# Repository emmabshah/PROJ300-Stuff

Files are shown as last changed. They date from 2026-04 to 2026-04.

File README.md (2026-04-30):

This repository contains some of the main features of Freddy, specifically software-related aspects mentioned throughout the report. 

•	Custom Parrot Voice - contains Freddy's custom trained voice model

•	Final CAD STLs - contains all CAD STL files for Freddy

•	Freddy Main Code - contains the main Freddy script that runs on the Pi

•	General Proj Docs - contains past submitted Proj-related documents like Proposals, Powerpoints, etc

•	Loggeed Test Data - contains the logged data when testing Freddy

•	Porcupine - contains the custom 'Hey Freddy' wake-word model 

•	Servos - contains the servo calibration code

•	TextyMcSpeechy Linux Screenshots - contains all the Linux code used for TextyMcSpeechy to generate the voice

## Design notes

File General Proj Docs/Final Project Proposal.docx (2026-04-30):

Project Title: Wearable Robot Puppet with Eye-Blinking and Tracking using Computer Vision

Proposer: Self (in collaboration with an Arts University Plymouth Final Year Student)

Supervisor: Dena Bazazian

Objective:

- The main objective of this project is to design and develop an animatronic head for the Arts University students’ wearable puppet, inspired by a dragon-like creature.
- The ultimate goal is to bring their puppet to life through realistic moveable eyeballs and eyelids and a moveable beak which opens and closes using servos for actuation and computer vision for person-detection and tracking. The final design would be as one complete structure allowing ease for the student to place within their puppet.

Staged Deliverables (at least 4):

PASS (40%+):

To achieve a functioning physical prototype of the eyes, beak and eye covering and simulation of its expected movement. This includes:

- Fusion 360 CAD modelling and technical drawings of the eyes, beak, servo mounts, battery and microcontroller housings, and eye covering plate.
- Incorporating camera placement in the pupil/ above eye.
- Fusion 360 animating to simulate expected movement (blink, move eyeball, open and close beak).
- 3D-printing parts with iterative design documentation.
- Fitment check with artist’s puppet structure.

2:2 Mark (50%+)

To achieve mechanical actuation of motion. This includes:

- Calibrating servos.
- Servo mapping and forward kinematics.
- Programming servo movement to make:
  - Eyes blink (1DOF)
  - Eyeballs move (2DOF)
  - Beak open and close (1DOF)
- Controlling the movement on ESP32 microcontrollers and PWM drivers.
- Creating a standard looped movement sequence for the eyes and beak. This is intended to be used in more crowded environments.

2:1 Mark (60%+)

To achieve person-detection with the vision system. This includes:

- Operating the ESP32-CAM modules.
- Person-detection using computer vision.
- Testing across different lighting.
- Sending data to ESP32 board.

FIRST CLASS Mark (70%+)

To achieve full integration of both the mechanical and vision system. This includes:

- Mapping camera data to servo movements to allow eye tracking of people.
- Independent tracking for each eye (since they sit on opposite sides of the head).
- Additional enhancements such as synchronized sound with beak motion or refined eye movement mimicking the expression of the person being tracked.
- Professional finish and detailed documentation of design process and testing.
- Have the option of controlling the eyes via joystick.

Description:

This project aims to combine robotics, art, and performance by creating a wearable robotic puppet head that responds dynamically to people. The system will feature realistic eye blinking, motion tracking, and beak articulation, controlled through small servos and ESP32 microcontroller.

Initially, CAD software (Fusion 360) will be used to design the eye and beak mechanisms. After simulation and refinement, parts will be 3D printed with PLA and assembled with servo mounts and control boards using various nuts and bolts. These will also undergo further refinement after fit checks.

The eyeballs themselves will move in 2DOF (up and down and left and right) and the eye lids which open and close (1 DOF). These would be actuated using 4 9g micro servos per eye. Each eye will be able to move independently. Their movement would be controlled using the PCA9685 PWM driver and ESP32 board.

It is intended that eyeball module is separate from one another, meaning each eye will have a dedicated ESP32, ESP32CAM, PWM driver, 4 servos and its own battery supply. The battery will potentially be a 6V battery pack but depending on the amount of current taken by the servos through testing, other means such as a Lipo and buck converter can be used.

The beak will also be actuated using one servo to open and close it, but this will potentially need a heavier MG996R servo for actuation. If the lighter micro servo will suffice, then that will be used instead.

The ESP32-CAM modules will enable person detection. The camera will be placed in the eyeball pupil or above the eyeball. The ESP32-CAM will send data to the ESP32, which will then send the mappings to the PWM driver, allowing the puppet’s eyes to follow a person’s movement.

All code will be developed in Arduino IDE, and iterative testing will be conducted. The final system will be designed for easy integration into an artist’s wearable puppet, allowing them to animate their creature during live performance.

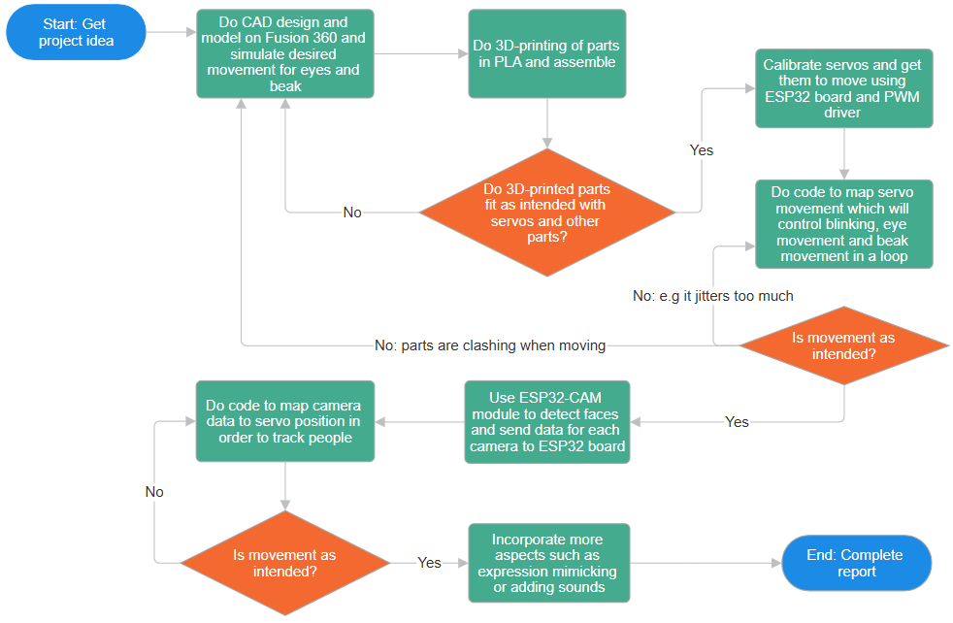
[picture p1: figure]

Figure 1: Flowchart Diagram of Project

Resources

- State assumptions about resources allocated to this project: Assume resources can be purchased within budget of £120.00
- Equipment: Power supply for testing, Laptop for CAD, 3D-printer for parts
- Locations: Lab
- Support & outside services: Lab techs
- Manufacturing: Not required

Schedule

- Deliverable 1 (Design and Simulation): By start of February (09/02/26)
- Deliverable 2 (Servo Actuation and Coding): By end of February (25/02/26)
- Progress Demonstration: February 26th, 2026
- Deliverable 3 (Vision System Integration): By middle of March (16/03/26)
- Deliverable 4 (Full Integration and Testing): By middle of April (13/04/26)

Related Documents

- Data Sheets:
1) 9G Micro Servos
- Web Pages: More to be included as research continues
1) Building a Robot that Sees (Through its Own Eyes): https://www.youtube.com/watch?v=IPBu5Q2aogE
2) Plymouth Owl: https://www.plymouth.ac.uk/research/robotics-neural-systems/plymouth-owl

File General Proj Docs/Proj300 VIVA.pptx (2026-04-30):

## PROJ300 VIVA

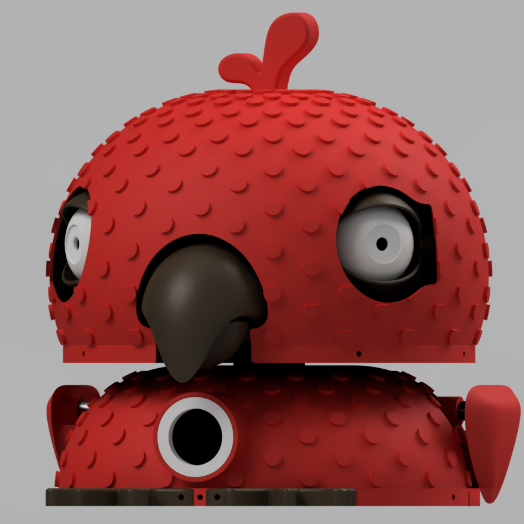
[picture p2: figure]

Interactive Parrot Robot with Face Tracking, Emotion Recognition and Voice Repetition
By Emma Shah

## Project Aim

Freddy was also designed to operate locally on the Raspberry Pi rather than relying on cloud services. This supported privacy, accessibility, and independence from internet connection.

- To create a characteristic animatronic robot that could:
- track a person’s face
- react to facial expressions
- listen for “Hey Freddy”
- repeat speech in a custom parrot voice
- move eyes, eyelids, wings, neck, beak, and LEDs

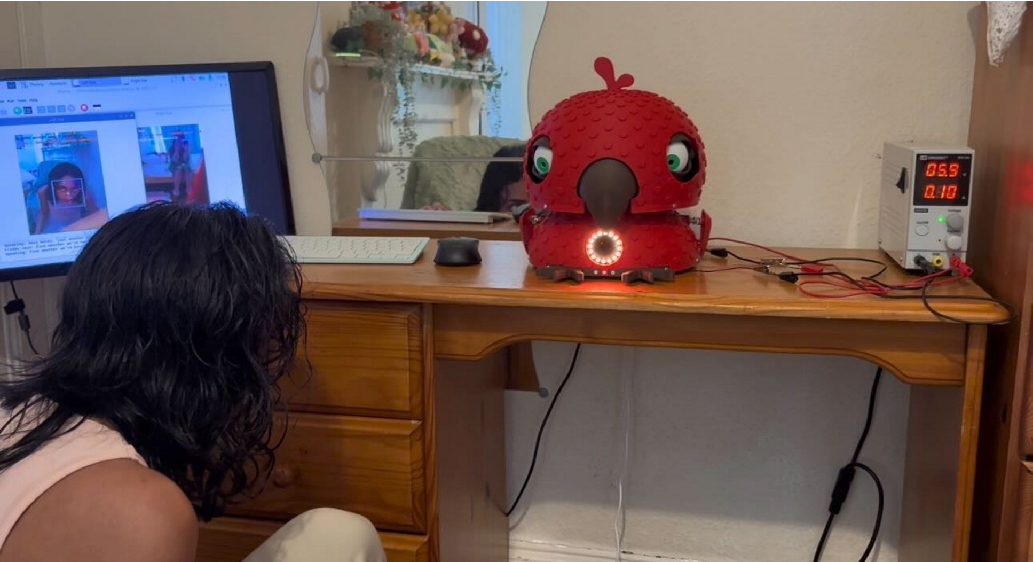
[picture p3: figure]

## Original vs Final Deliverables

Proposal stage | Original target | Final outcome
Pass | Physical prototype of eyes, beak, covering, CAD simulation, 3D prints, fitment checks | Achieved and expanded into a full animatronic parrot body with eyes, eyelids, beak, wings, neck, covering, fitment checks, CAD simulations, and final assembly
2:2 | Servo calibration and programmed motion for blinking, eyeball movement, and beak actuation | Achieved, with additional servo-driven wings, neck movement, beak animation, eyelids, and emotion-based motion behaviours
2:1 | Person detection using ESP32-CAM modules and testing in different lighting | Achieved using Raspberry Pi 5 and dual Pi cameras instead of ESP32-CAMs, with MediaPipe face detection and testing under different lighting/movement conditions
First | Camera data mapped to servo movement for independent eye tracking, plus enhancements such as sound/beak synchronisation and expressive behaviour | Achieved and expanded: face tracking controlled eyes and neck, while additional systems included emotion recognition, wake-word detection, speech transcription, custom Piper voice, beak animation, LEDs, and parrot mode

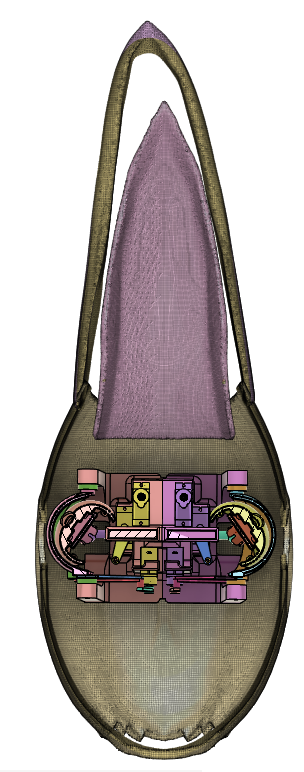
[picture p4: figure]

## System Overview

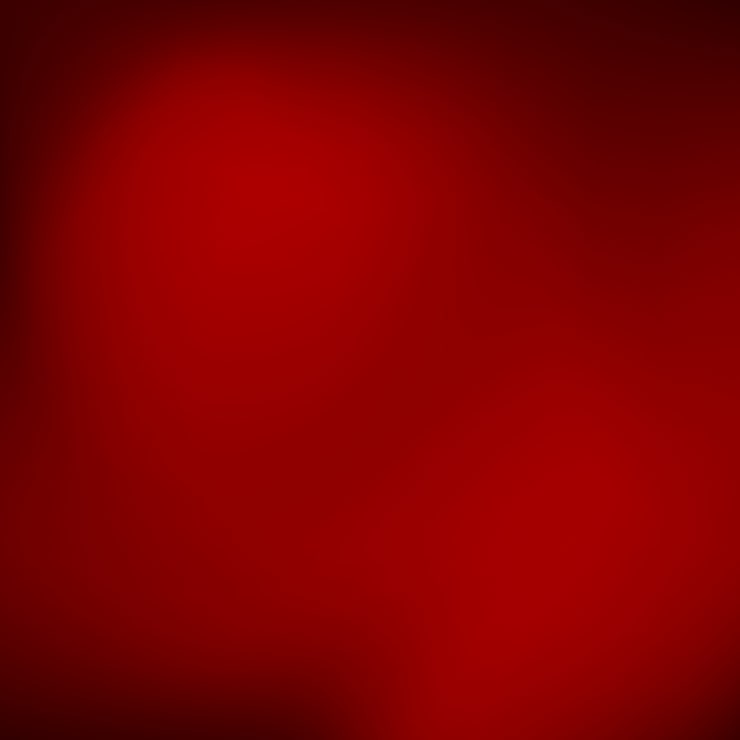
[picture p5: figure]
Red backdrop background Images - Free Download on Freepik
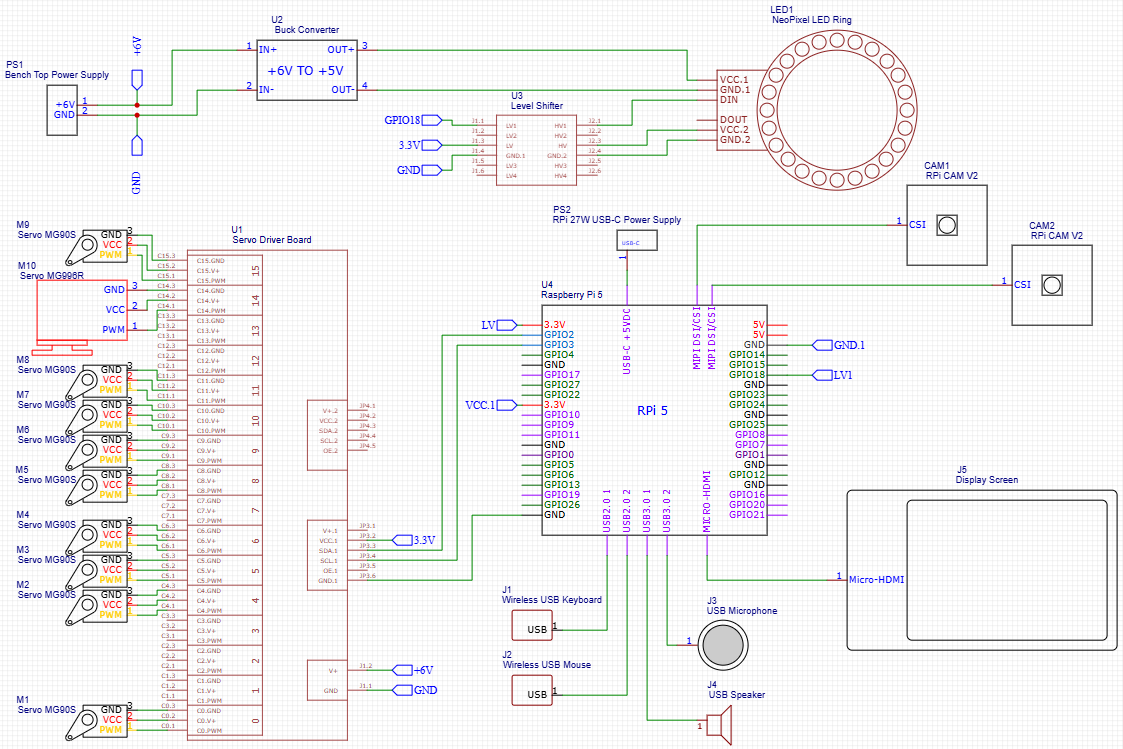
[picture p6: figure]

Freddy was built around a Raspberry Pi 5, which coordinated the vision, audio, and motion subsystems. Key components included:
- Two Raspberry Pi Camera Module 2 for face tracking
- A PCA9685 driver board for servo control
- Servos for the eyes, eyelids, beak, wings, and neck
- A NeoPixel LED ring for emotion feedback
- A microphone for wake-word detection and speech input
- A speaker for audio output
- Power regulation components including a buck converter
- Bi-directional logic level shifter to convert Pi 3.3V data output to 5V

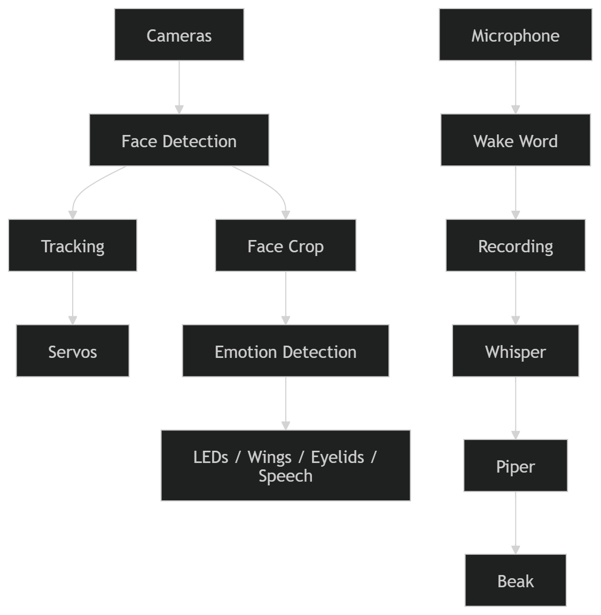
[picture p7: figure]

## Mechanical Design

Freddy was design in Fusion 360 and 3D-print in PLA. Most parts were 3D printed and designed from scratch.
The design involved:

- MG90S servo-driven eyes, eyelids, beak and wings
- MG996R servo-driven neck
- Mounts for the Pi, PCA9685, Speaker, Buck Convertor, Microphone
The design was the longest process as it involved lots of iteration through physical fitment tests.

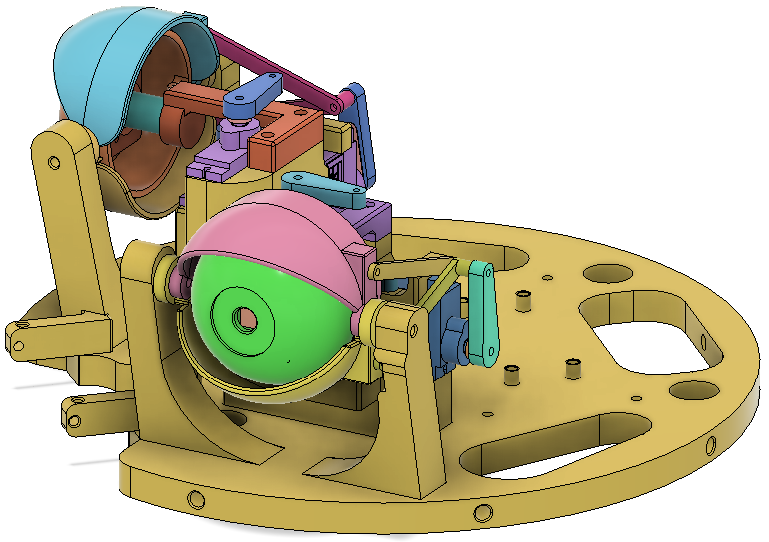
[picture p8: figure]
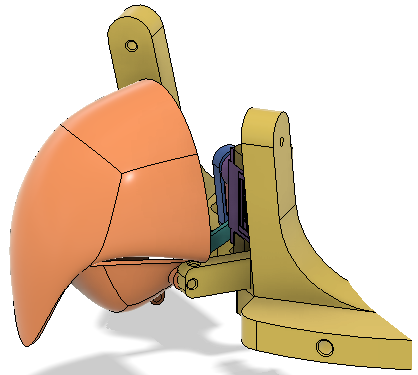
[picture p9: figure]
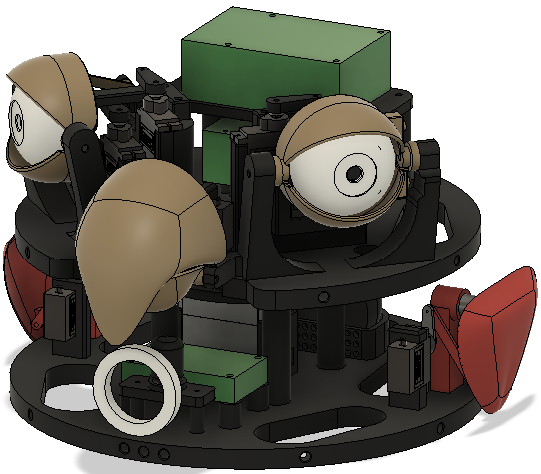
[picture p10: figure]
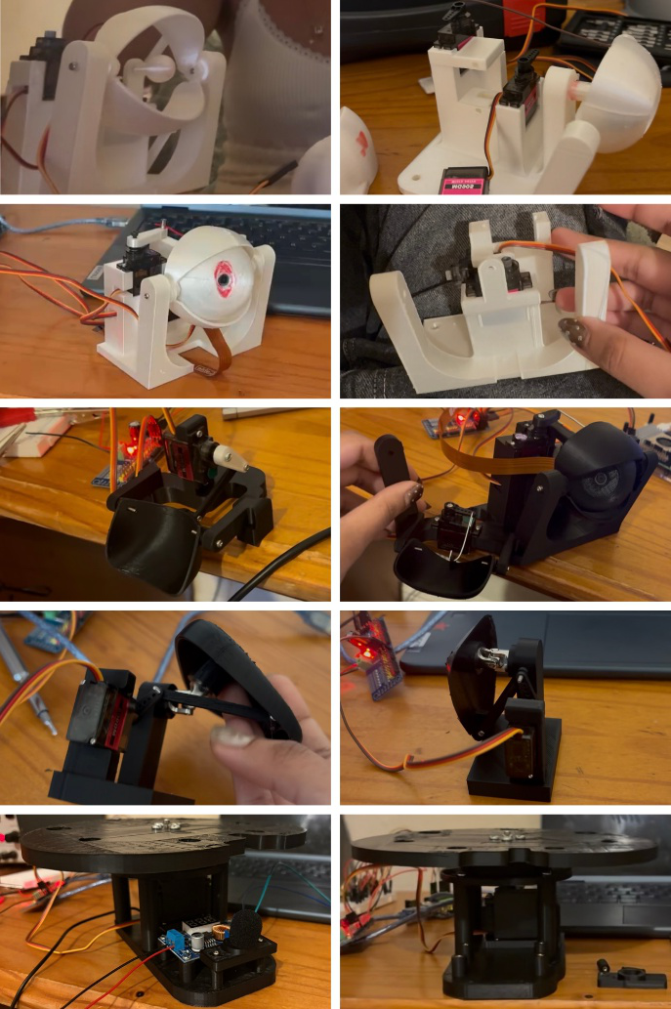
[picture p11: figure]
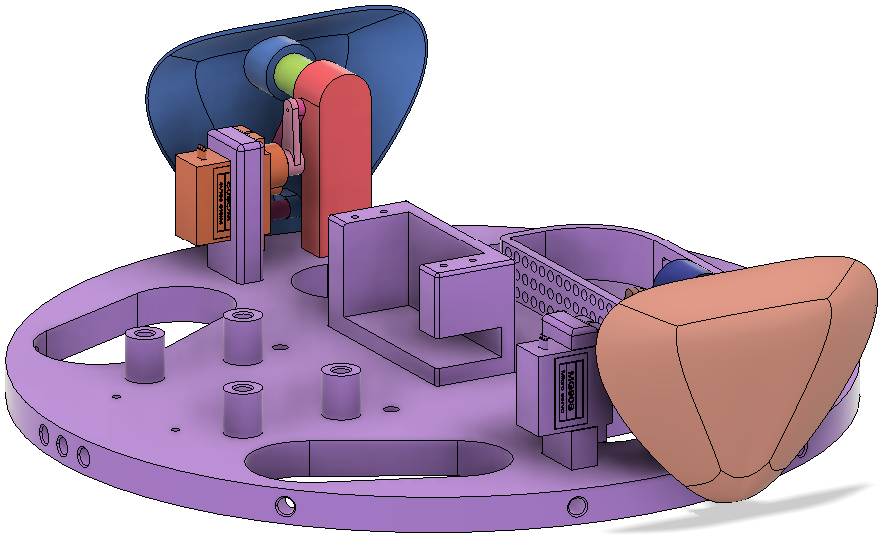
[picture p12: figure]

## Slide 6

Servo Calibration

Since servos do not know their true position, they had to be calibrated using a protractor to determine 0-180° motion.
Pulse Width Modulation (PWM) tick limits for each mechanism had to be found experimentally. An Arduino UNO, PCA9685 and potentiometers were used to do this, and final calibrated values were transferred into Python on the Pi.

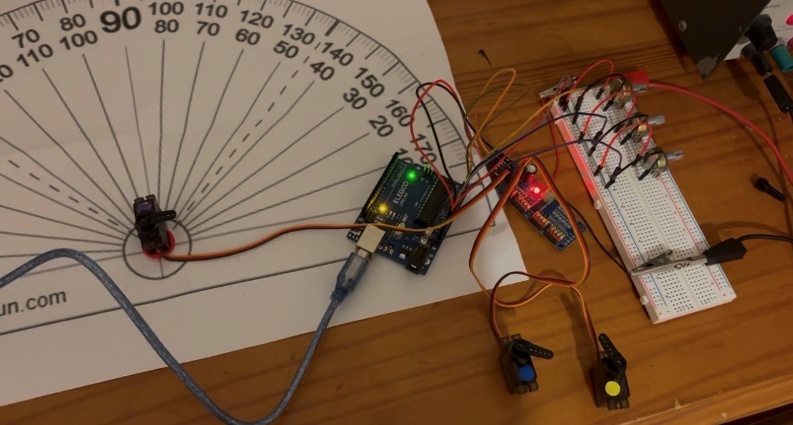
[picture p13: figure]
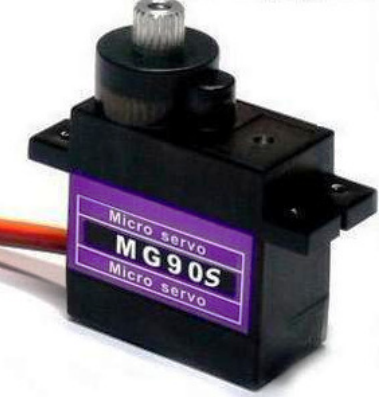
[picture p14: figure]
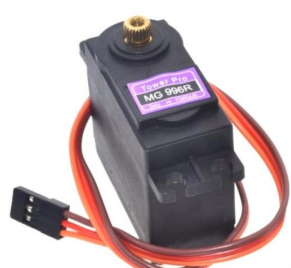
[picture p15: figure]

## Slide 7

Face Tracking

Freddy uses the cameras mounted as pupils in its eyeballs to track. It incorporates active target selection, proportional-style tracking, deadzones to reduce jitter and scanning when no face is detected.
For face detection, MediaPipe, an open-source framework from Google, was used. When a face was detected in the camera frame, the code compared that position to the centre of the frame and then moved the eyes and neck to reduce the error between the two.

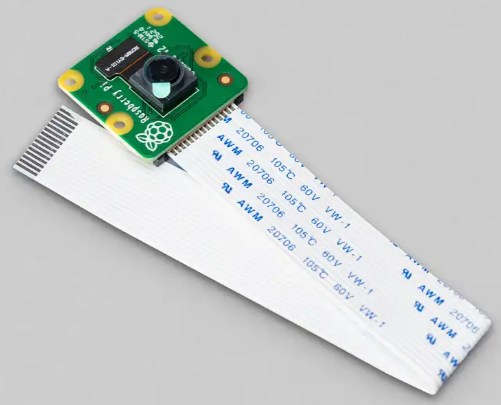
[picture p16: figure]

Testing:
With the confidence threshold = 0.5,
The tracking solution performed well with a normalised tracking error of 0.287 maximum and only 4 instances in which the face was not detected.

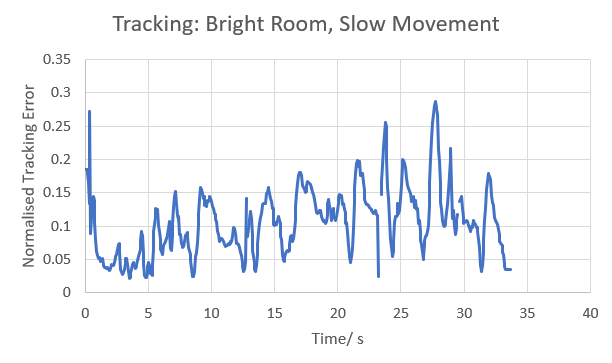
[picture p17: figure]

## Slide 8

Emotion Recognition

Freddy uses another open-source framework for emotion recognition: HSEmotion, specifically the model, enet_b0_8_best_afew. He can detect 7 out of the 8 emotions: happy, sad, angry, disgust, fear, surprise, neutral.

timestamp | raw_prediction | stable_emotion
1777036530 | disgust | neutral
1777036531 | disgust | neutral
1777036532 | disgust | disgust
1777036533 | disgust | disgust
1777036534 | disgust | disgust
1777036535 | disgust | disgust
1777036536 | disgust | disgust
1777036537 | disgust | disgust
1777036538 | disgust | disgust
1777036539 | disgust | disgust
1777036540 | disgust | disgust
1777036541 | disgust | disgust
1777036542 | disgust | disgust
1777036543 | disgust | disgust
1777036544 | disgust | disgust
1777036545 | disgust | disgust
1777036546 | angry | disgust
1777036547 | disgust | disgust
1777036548 | disgust | disgust
1777036549 | disgust | disgust

Essentially, a cropped face is passed to the model, raw predictions could flicker but with a confidence threshold, majority voting, and stability timer, behaviour was smoother.
Testing:
For an example of the stability working, this was a snippet of test data when detecting ‘disgust’.

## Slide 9

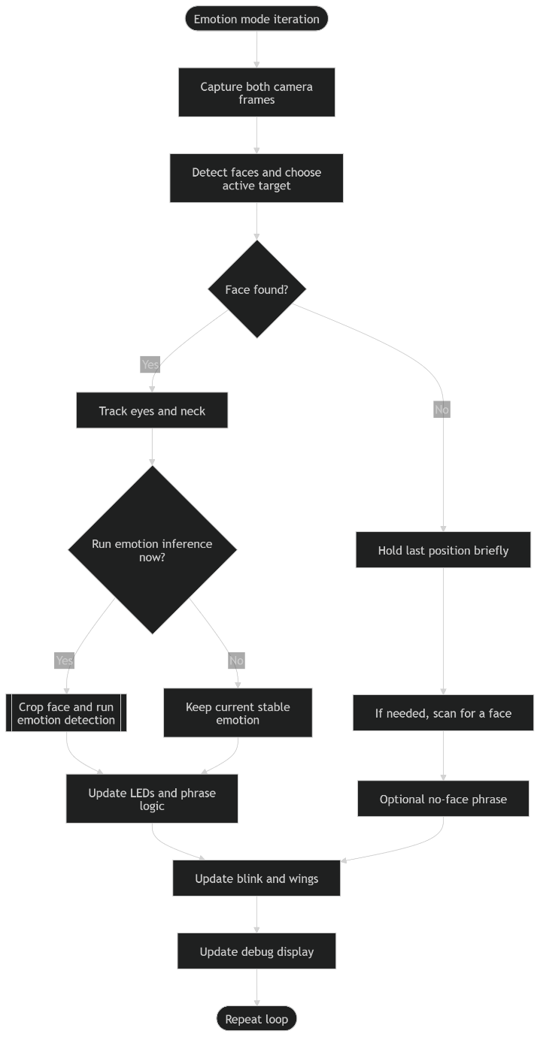
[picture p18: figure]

Modes

Freddy has two distinct modes of interaction:
1. Robot/ Emotion Mode: Freddy tracks the user’s face, recognises their emotion then responds with eyelid and wing movement, speech, and LED ring colour changes.
2. Parrot Mode: Freddy listens for the wake-word, “Hey Freddy”, transcribes spoken input with Whsiper STT, translates it into English, and repeats it aloud with Piper TTS.
Testing:
A big challenge with Freddy being local and offline, meant that latency was a potential issue. After testing, the Base Whisper Model was found to perform best in terms of balancing accuracy and latency, performing at 73% English transcription accuracy and approximately 4s transcription time.
Translation was still quite inaccurate though with a 30% accuracy.

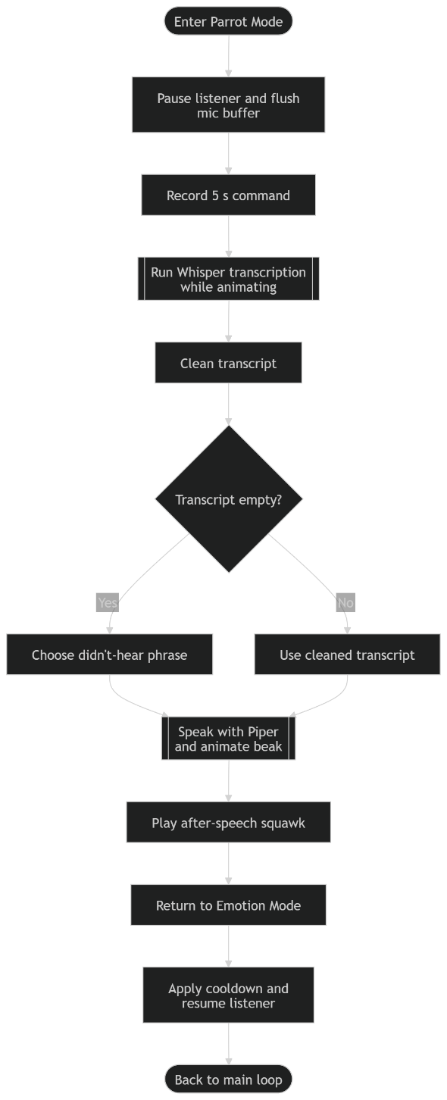
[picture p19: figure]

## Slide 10

Custom Voice

- ElevenLabs used was to establish desired voice style
- Chatterbox TTS was used to generated 1500 training clips from a metadata.csv file using the selected voice
- Training clips were manually checked
- An open-source framework, TextyMcSpeechy, was used to train the custom Piper voice for 5 hours
- Final voice model ran locally and offline

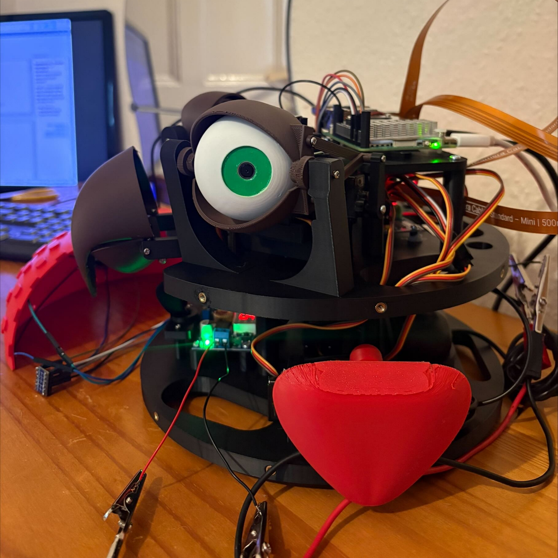
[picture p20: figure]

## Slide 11

Wake-word Detection

A framework called by Picovoice called Porcupine was used to generate the custom wake-word model, ‘Hey Freddy’.
Testing:
A sensitivity of 0.8 worked well for detection but false positives still existed with a 30% false positive detection rate.

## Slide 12

Why these models?

Component | Chosen option | Why
Face detection | MediaPipe | lightweight, real-time, gives bounding boxes
Emotion | HSEmotion | pre-trained, easier than training from scratch
STT | Whisper Base | best accuracy/ latency compromise
TTS | Piper | lightweight, local/ offline TTS
Wake word | Porcupine | more reliable than openWakeWord which was previously used

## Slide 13

Challenges

- Integrating many threaded subsystems: race conditions
- Servo calibration: tedious
- Cable routing issue: restricting neck motion
- Custom voice training: time-consuming
- Debugging hardware/ software together: figuring out whether servo jitter was code-related or a mechanical issue
- False wake-word triggers
- Latency and poor translation

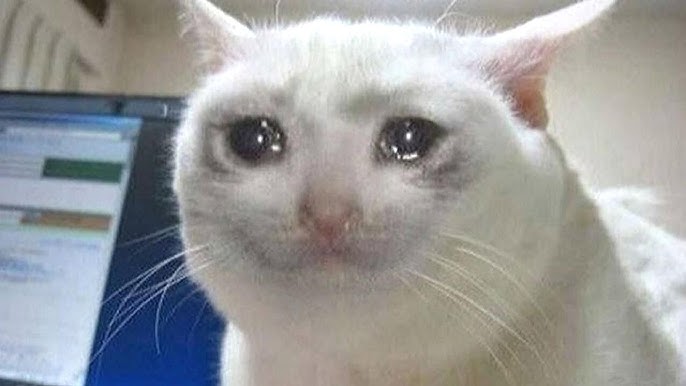
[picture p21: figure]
Sad Cats - Cute & Funny Cat Videos Compilation

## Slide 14

What I Learned

- New aspects about Fusion 360 CAD: forms, motion studies, tolerances, drawings
- How to use a 3D-printer: fitment check
- How to use a Raspberry Pi for a robotics project
- Linux, virtual environments, terminal commands, and dependency installation
- Experience in integrating pre-trained ML models
- Improved confidence in handling unfamiliar technical problems

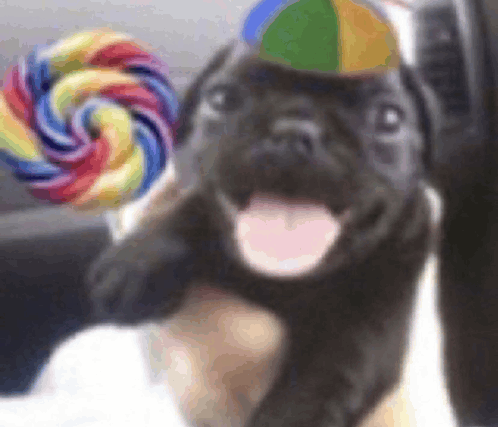
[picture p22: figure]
Happy Dog With A Lollipop Meme - Happy dog with a lollipop - Discover & Share GIFs

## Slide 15

Future Improvements

- Get a better microphone
- AI accelerator HAT for faster offline models
- Modular code structure rather than one giant script
- Raspberry Pi-based servo calibration script
- Better neck cable routing
- Physical start/ stop button
- Belly LCD display for transcription/ status
- Voice activity detection instead of fixed 5s recording
- Possible local LLM for replies instead of pre-determined phrases

## Demo

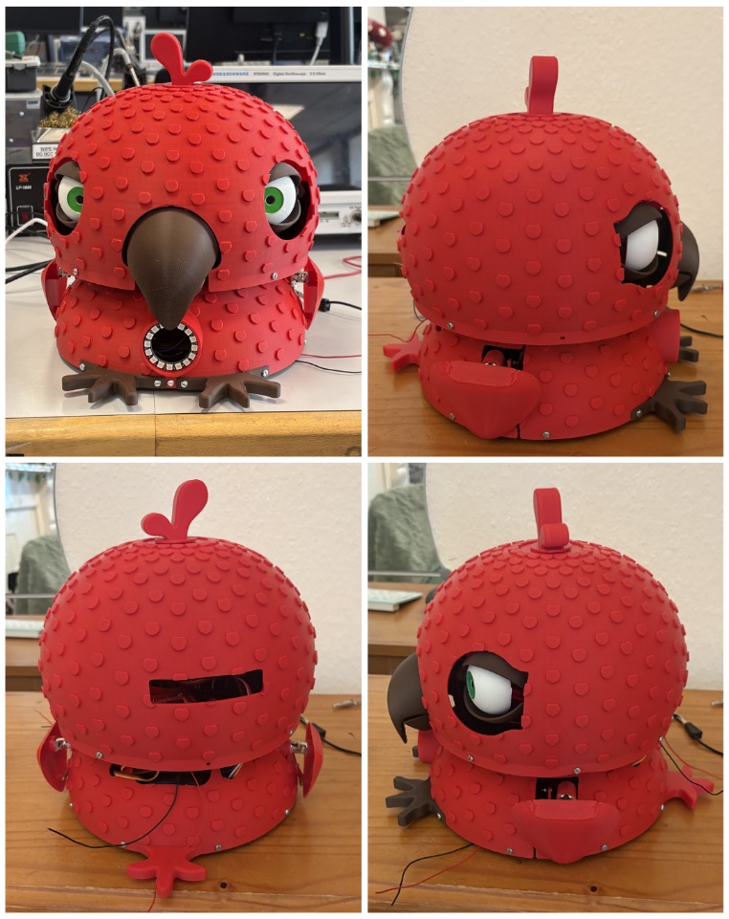
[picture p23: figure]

## Feedback

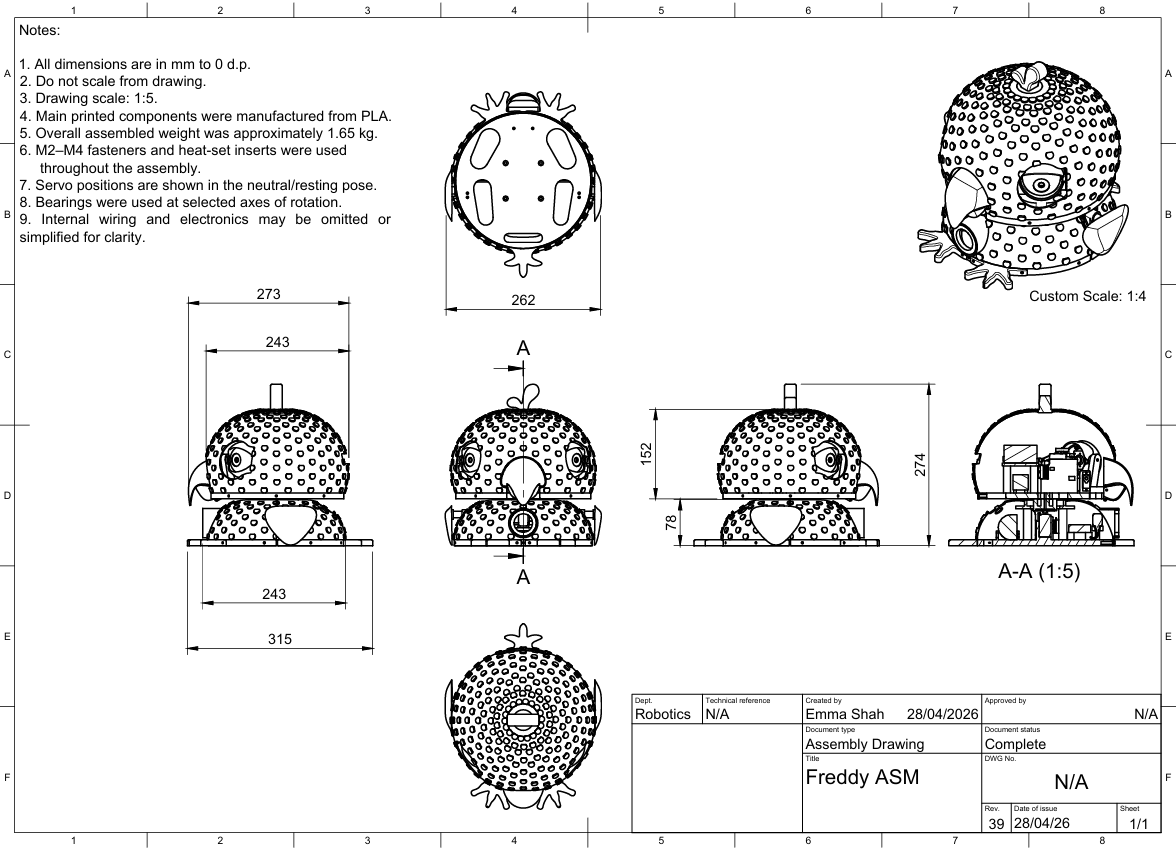
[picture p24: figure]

If you have any questions, please do let me know!

## THANK YOU

Emma Shah

1,600+ Smiley Face Thumbs Up Stock Photos, Pictures & Royalty-Free Images - iStock | Smiley face icon

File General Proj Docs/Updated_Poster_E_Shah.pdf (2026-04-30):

# IInntteerraaccttiivveePPaarrrroottRRoobboott

wwiitthhFFaacceeTTrraacckkiinngg,,EEmmoottiioonnRReeccooggnniittiioonnaannddVVooiicceeRReeppeettiittiioonn

# “Hey Freddy”

# “Hey Freddy”

Emma Shah
emmabshah@gmail.com

BEng (Hons) Robotics, University of Plymouth Dena Bazazian (Supervisor) www.linkedin.com/in/emmabshah

### Overview

Freddy is an interactive parrot-inspired animatronic robot that runs locally and offline on a Raspberry Pi 5. Designed in Fusion 360, built using 3D-printed parts, and actuated with MG90S and MG996R servos, Freddy aims to provide engaging entertainment and educational interaction without relying on cloud services.

### Overview

Freddy is an interactive parrot-inspired animatronic robot that runs locally and offline on a Raspberry Pi 5. Designed in Fusion 360, built using 3D-printed parts, and actuated with MG90S and MG996R servos, Freddy aims to provide engaging entertainment and educational interaction without relying on cloud services.

### Technical Features

Freddy was coded in Python, using open-source libraries such as MediaPipe for face detection, HSEmotion for emotion recognition, and Whisper for speech-to-text transcription. It also uses a custom Piper voice for text-tospeech, trained on ElevenLabs-generated audio. Additionally, the wake-word model was generated using Porcupine.

### Technical Features

Freddy was coded in Python, using open-source libraries such as MediaPipe for face detection, HSEmotion for emotion recognition, and Whisper for speech-to-text transcription. It also uses a custom Piper voice for text-tospeech, trained on ElevenLabs-generated audio. Additionally, the wake-word model was generated using Porcupine.

### How to Interact with Freddy

### 1. Robot Mode (Default): Freddy tracks the user’s face using two

Raspberry Pi Camera Module 2 cameras mounted in its eyes and recognises seven emotions. It then responds with eyelid and wing movement, speech, and LED ring colour changes.

### 2. Parrot Mode: Freddy listens for a wake word, transcribes spoken

input, translates it into English, and repeats it aloud. Simply say “Hey Freddy” to activate Parrot Mode.

### How to Interact with Freddy

### 1. Robot Mode (Default): Freddy tracks the user’s face using two

Raspberry Pi Camera Module 2 cameras mounted in its eyes and recognises seven emotions. It then responds with eyelid and wing movement, speech, and LED ring colour changes.

### 2. Parrot Mode: Freddy listens for a wake word, transcribes spoken

input, translates it into English, and repeats it aloud. Simply say “Hey Freddy” to activate Parrot Mode.

Buck Converter, Level Shifter, MG90S and PCA9685 Images from Amazon.com Raspberry Pi 5 and Raspberry Pi Camera Module 2 Images from ThePiHut.com

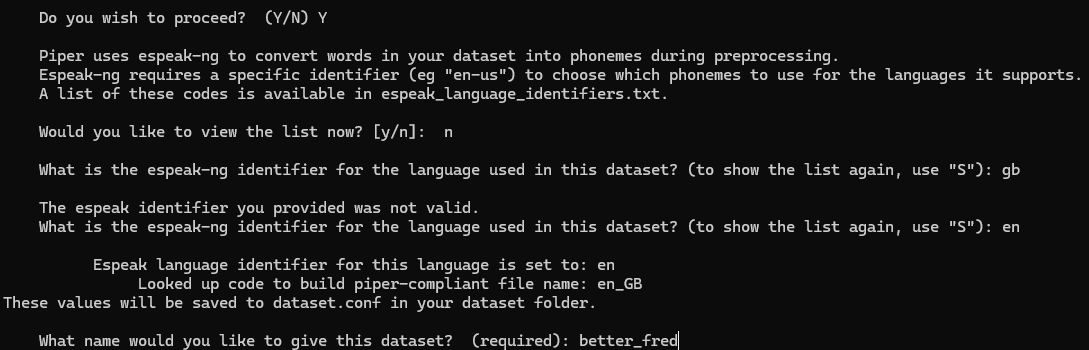
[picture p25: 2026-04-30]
TextyMcSpeechy Linux Screenshots/Screenshot21.png

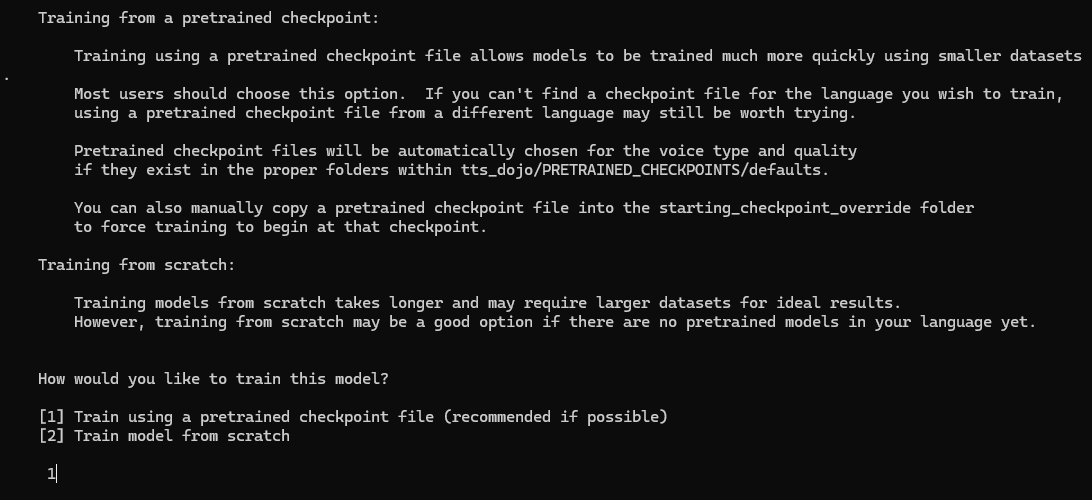
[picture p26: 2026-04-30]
TextyMcSpeechy Linux Screenshots/Screenshot30.png

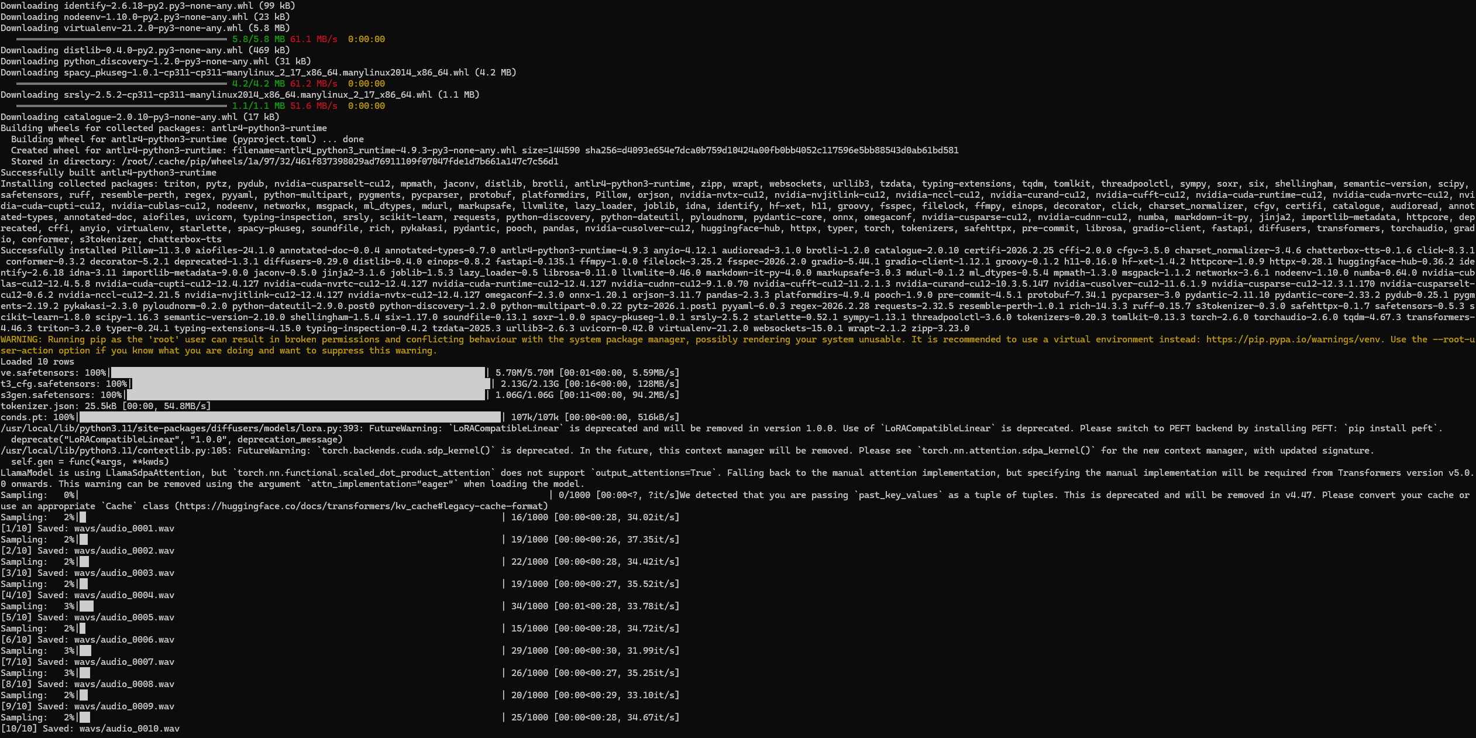
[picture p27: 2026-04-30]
TextyMcSpeechy Linux Screenshots/Screenshot5.png

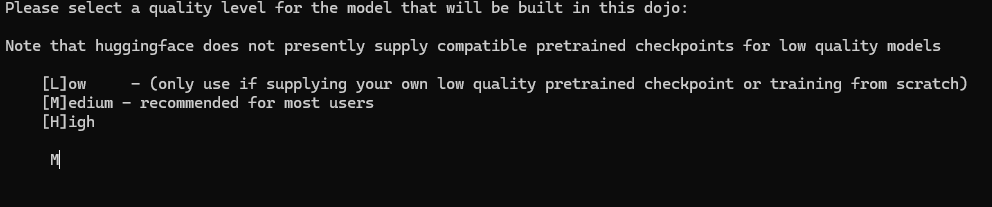
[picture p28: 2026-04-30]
TextyMcSpeechy Linux Screenshots/Screenshot29.png

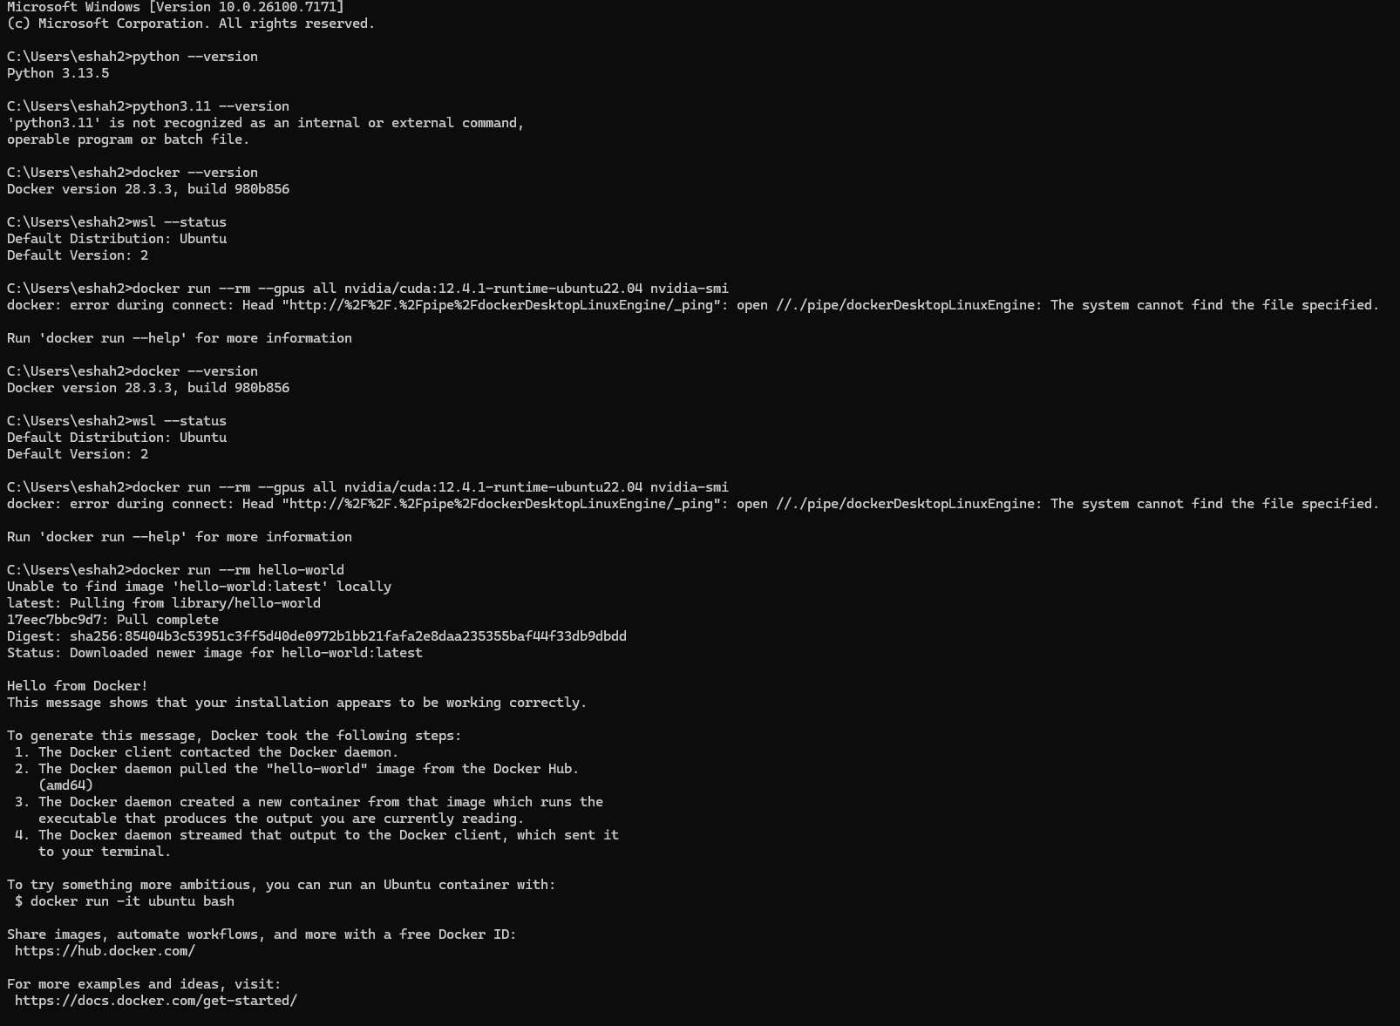
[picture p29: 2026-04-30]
TextyMcSpeechy Linux Screenshots/Screenshot1.png

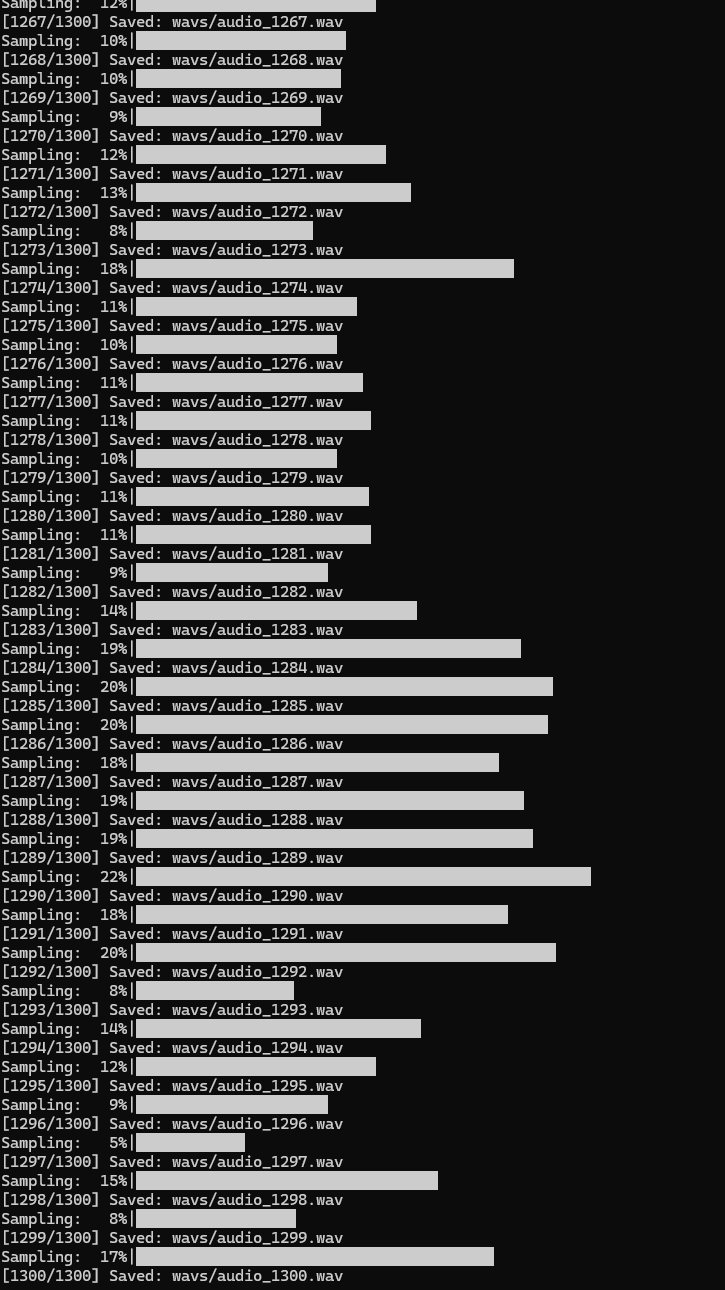
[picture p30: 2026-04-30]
TextyMcSpeechy Linux Screenshots/Screenshot6.png

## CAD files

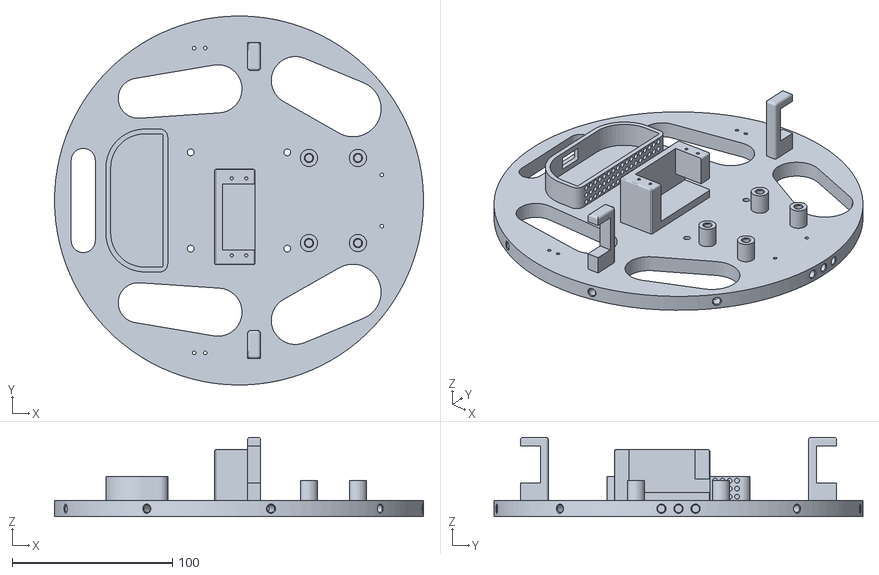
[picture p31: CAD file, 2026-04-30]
Final CAD STLs/Black or whatever colour/Body base.stl
230.0 x 230.0 x 49.5

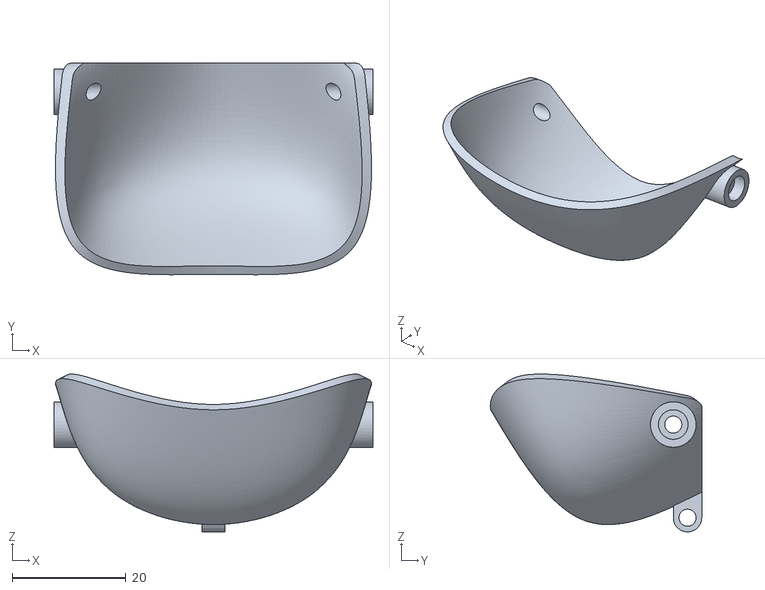
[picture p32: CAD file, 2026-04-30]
Final CAD STLs/Brown/Bottom beak.stl
56.0 x 37.1 x 27.7

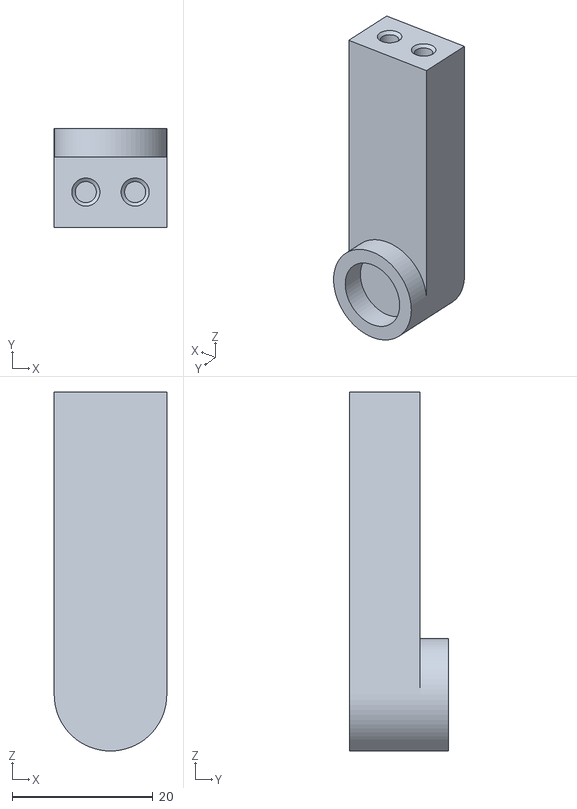
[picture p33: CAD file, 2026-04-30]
Final CAD STLs/Red/Wing joint holder (x2).stl
16.0 x 14.0 x 51.0

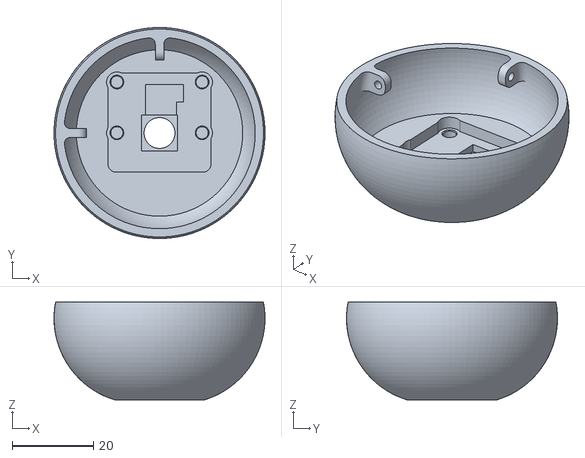
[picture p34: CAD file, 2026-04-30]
Final CAD STLs/White/Right eyeball.stl
52.0 x 52.0 x 24.1

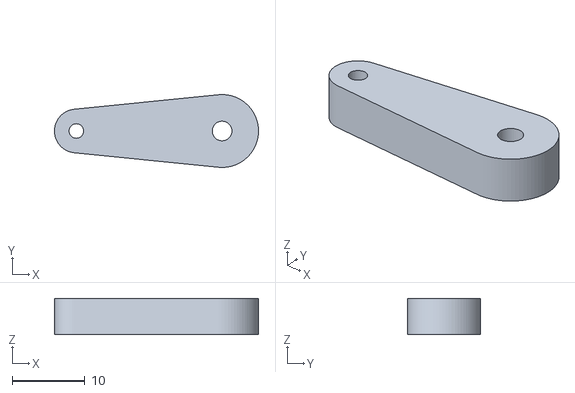
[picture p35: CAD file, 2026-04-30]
Final CAD STLs/Black or whatever colour/Servo horn extender short (x4).stl
28.0 x 10.00 x 5.00

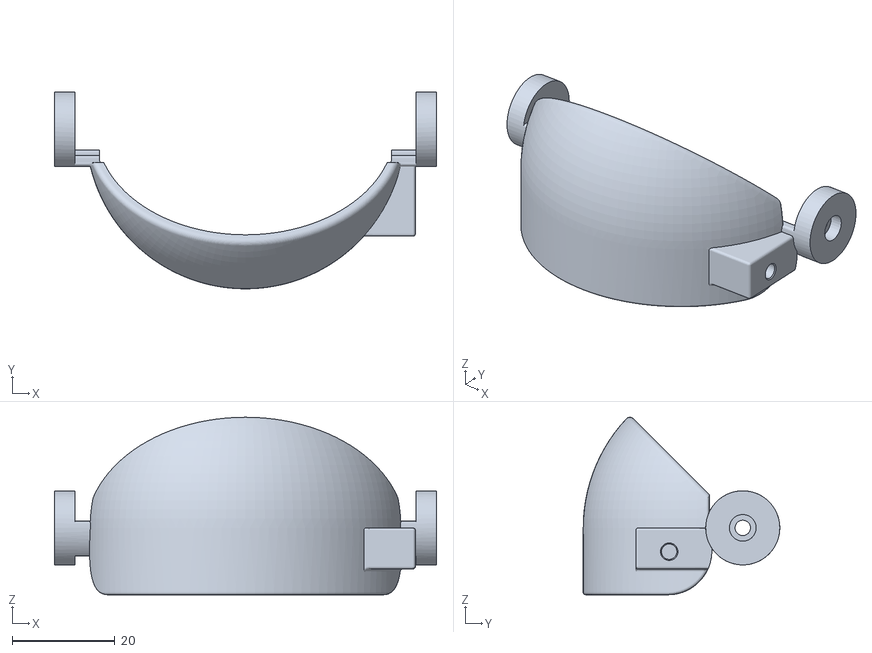
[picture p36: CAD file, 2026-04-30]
Final CAD STLs/Brown/Left lower eyelid.stl
74.2 x 38.2 x 34.5

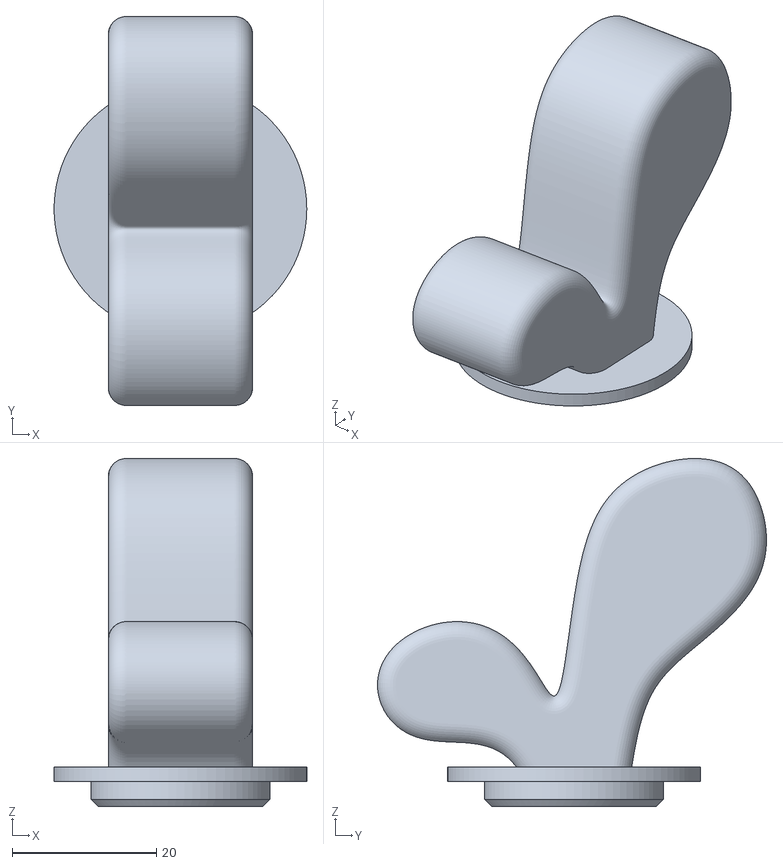
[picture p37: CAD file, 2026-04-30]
Final CAD STLs/Red/Top head feather.stl
35.0 x 53.9 x 48.2

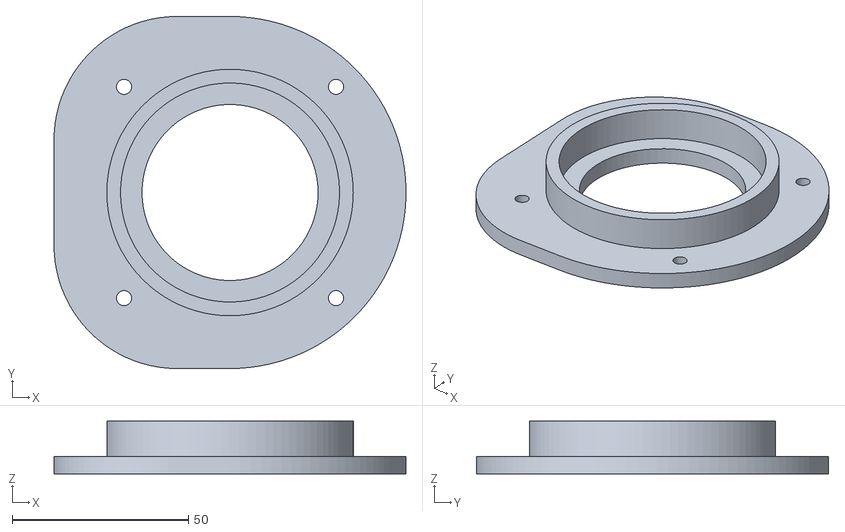
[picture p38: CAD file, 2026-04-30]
Final CAD STLs/Black or whatever colour/Neck bearing holder.stl
100.0 x 100.0 x 15.0

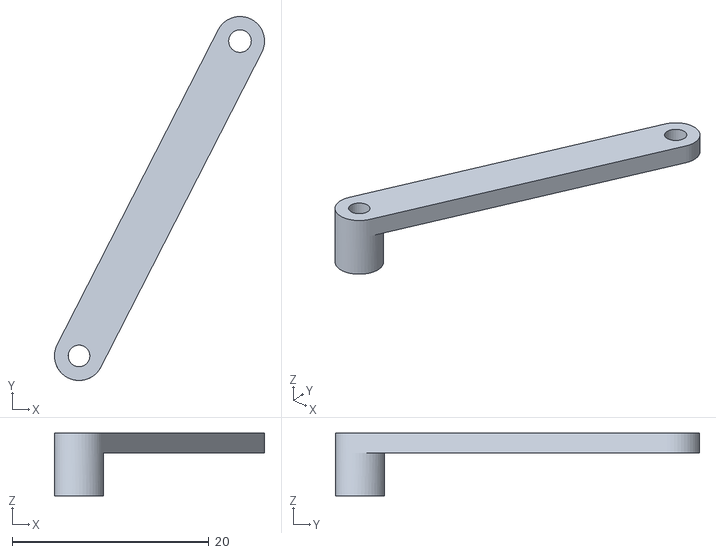
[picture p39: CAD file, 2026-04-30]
Final CAD STLs/Brown/Bottom beak link.stl
21.3 x 37.0 x 6.39

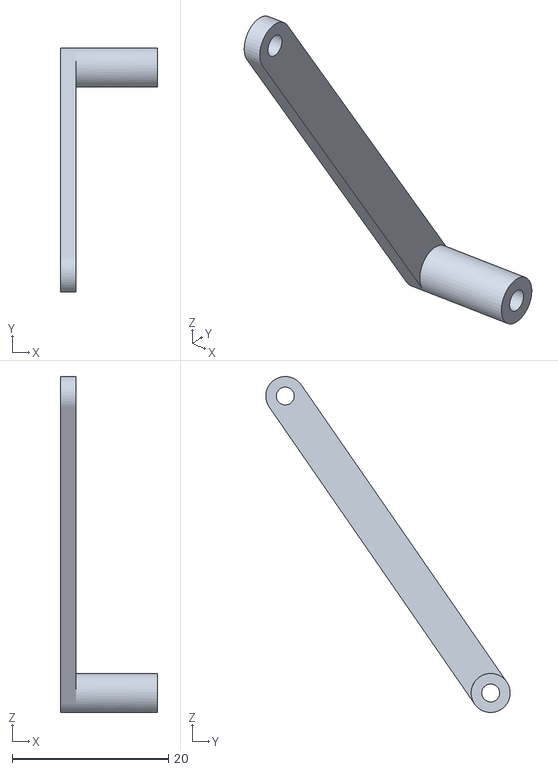
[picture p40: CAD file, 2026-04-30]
Final CAD STLs/Red/Wing link (x2).stl
12.5 x 31.3 x 43.0

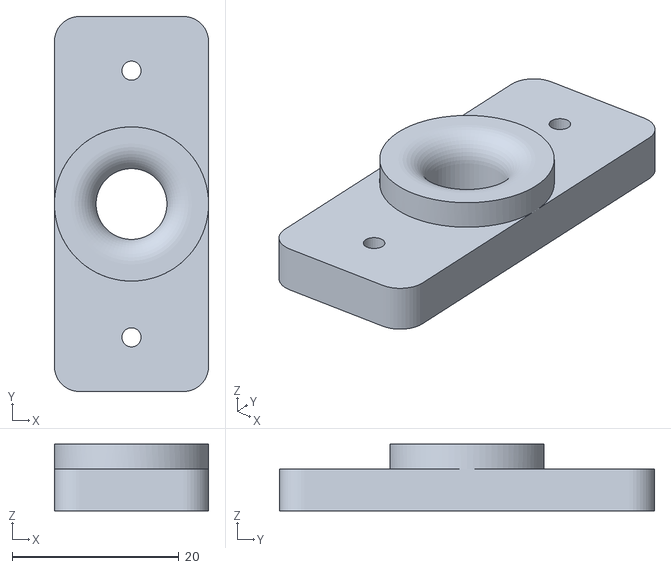
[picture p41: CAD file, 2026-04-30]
Final CAD STLs/Black or whatever colour/Mic holder.stl
18.5 x 45.0 x 8.00

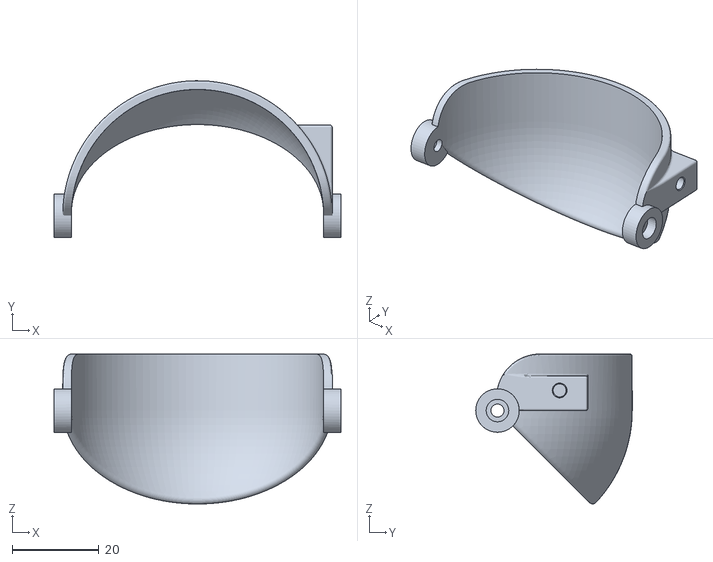
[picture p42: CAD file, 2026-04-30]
Final CAD STLs/Brown/Right upper eyelid.stl
66.0 x 36.0 x 34.5

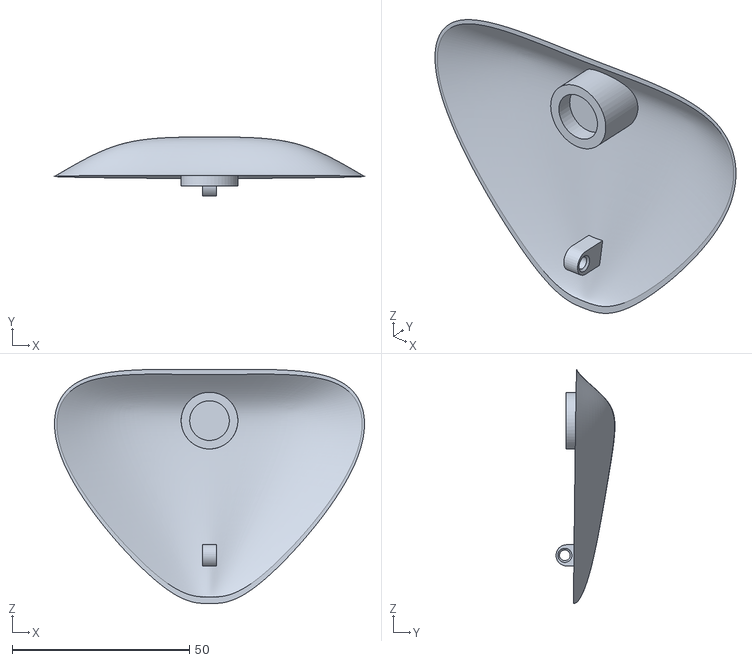
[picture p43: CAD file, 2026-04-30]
Final CAD STLs/Red/Left wing.stl
87.5 x 16.6 x 66.1

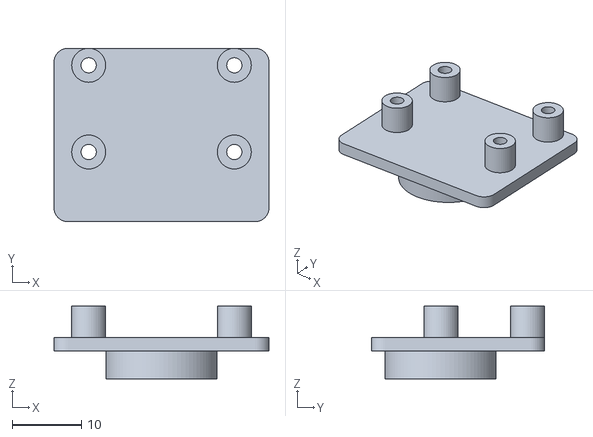
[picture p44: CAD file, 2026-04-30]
Final CAD STLs/Black or whatever colour/Eye joint holder (x2).stl
31.0 x 25.0 x 10.5

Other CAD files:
Final CAD STLs/White/Left eyeball updated.stl
Final CAD STLs/Brown/Right foot updated.stl
Final CAD STLs/Red/Right wing.stl
Final CAD STLs/Black or whatever colour/Servo horn extender middle (x2).stl
Final CAD STLs/Black or whatever colour/Body cylinder (4x).stl
Final CAD STLs/Black or whatever colour/Head cylinder (4x).stl
Final CAD STLs/Black or whatever colour/Head plate.stl
Final CAD STLs/Black or whatever colour/Left joint holder.stl
Final CAD STLs/Black or whatever colour/Mic cylinder (x2).stl
Final CAD STLs/Black or whatever colour/Neck cylinder update V2.stl
Final CAD STLs/Black or whatever colour/Neck cylinder.stl
Final CAD STLs/Black or whatever colour/Pi plate.stl
Final CAD STLs/Black or whatever colour/Right joint holder.stl
Final CAD STLs/Brown/Bottom eye link (x2).stl
Final CAD STLs/Brown/Left foot updated.stl
Final CAD STLs/Brown/Left upper eyelid.stl
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

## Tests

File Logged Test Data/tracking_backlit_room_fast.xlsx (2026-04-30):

timestamp | elapsed_s | condition | active_cam | has_face | face_x | face_y | centre_x | centre_y | error_x | error_y | error_dist | norm_error_dist | frame_w | frame_h | l_pan_norm | r_pan_norm | tilt_norm | neck_ticks
1777032181 | 0.001 | backlit_room_fast | L | TRUE | 124 | 200 | 240 | 320 | -116 | -120 | 166.9 | 0.2086 | 480 | 640 | 0.058 | 0 | -0.045 | 230 | MAX | 0.2086
1777032181 | 0.148 | backlit_room_fast | L | TRUE | 126 | 198 | 240 | 320 | -114 | -122 | 167 | 0.2087 | 480 | 640 | 0.115 | 0 | -0.0907 | 230
1777032181 | 0.19 | backlit_room_fast | L | TRUE | 126 | 195 | 240 | 320 | -114 | -125 | 169.2 | 0.2115 | 480 | 640 | 0.172 | 0 | -0.1376 | 230
1777032181 | 0.226 | backlit_room_fast | L | TRUE | 129 | 194 | 240 | 320 | -111 | -126 | 167.9 | 0.2099 | 480 | 640 | 0.2275 | 0 | -0.1849 | 230
1777032181 | 0.275 | backlit_room_fast | L | TRUE | 133 | 189 | 240 | 320 | -107 | -131 | 169.1 | 0.2114 | 480 | 640 | 0.281 | 0 | -0.234 | 230
1777032181 | 0.306 | backlit_room_fast | L | TRUE | 136 | 184 | 240 | 320 | -104 | -136 | 171.2 | 0.214 | 480 | 640 | 0.333 | 0 | -0.285 | 230
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

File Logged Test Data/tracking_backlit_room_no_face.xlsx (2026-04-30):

timestamp | elapsed_s | condition | active_cam | has_face | face_x | face_y | centre_x | centre_y | error_x | error_y | error_dist | norm_error_dist | frame_w | frame_h | l_pan_norm | r_pan_norm | tilt_norm | neck_ticks
1777032445 | 0.001 | backlit_room_no_face | none | FALSE |  |  |  |  |  |  |  |  |  |  | 0 | 0 | 0 | 230
1777032445 | 0.107 | backlit_room_no_face | none | FALSE |  |  |  |  |  |  |  |  |  |  | -0.0005 | -0.0005 | 0 | 230
1777032445 | 0.15 | backlit_room_no_face | none | FALSE |  |  |  |  |  |  |  |  |  |  | -0.0015 | -0.0015 | 0 | 229
1777032445 | 0.184 | backlit_room_no_face | none | FALSE |  |  |  |  |  |  |  |  |  |  | -0.0029 | -0.0029 | 0 | 228
1777032445 | 0.228 | backlit_room_no_face | none | FALSE |  |  |  |  |  |  |  |  |  |  | -0.0048 | -0.0048 | 0 | 228
1777032445 | 0.266 | backlit_room_no_face | none | FALSE |  |  |  |  |  |  |  |  |  |  | -0.007 | -0.007 | 0 | 228
1777032445 | 0.311 | backlit_room_no_face | L | TRUE | 312 | 216 | 240 | 320 | 72 | -104 | 126.5 | 0.1581 | 480 | 640 | -0.043 | -0.0067 | -0.039 | 228
1777032446 | 0.378 | backlit_room_no_face | none | FALSE |  |  |  |  |  |  |  |  |  |  | -0.043 | -0.0067 | -0.039 | 228
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

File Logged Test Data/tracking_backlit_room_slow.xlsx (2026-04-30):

timestamp | elapsed_s | condition | active_cam | has_face | face_x | face_y | centre_x | centre_y | error_x | error_y | error_dist | norm_error_dist | frame_w | frame_h | l_pan_norm | r_pan_norm | tilt_norm | neck_ticks
1777032124 | 0.002 | backlit_room_slow | L | TRUE | 129 | 147 | 240 | 320 | -111 | -173 | 205.5 | 0.2569 | 480 | 640 | 0.0555 | 0 | -0.0649 | 230
1777032124 | 0.14 | backlit_room_slow | L | TRUE | 127 | 141 | 240 | 320 | -113 | -179 | 211.7 | 0.2646 | 480 | 640 | 0.112 | 0 | -0.132 | 230 | MAX | 0.2891
1777032124 | 0.173 | backlit_room_slow | L | TRUE | 126 | 141 | 240 | 320 | -114 | -179 | 212.2 | 0.2653 | 480 | 640 | 0.169 | 0 | -0.1991 | 230
1777032124 | 0.214 | backlit_room_slow | L | TRUE | 124 | 140 | 240 | 320 | -116 | -180 | 214.1 | 0.2677 | 480 | 640 | 0.227 | 0 | -0.2666 | 230
1777032124 | 0.251 | backlit_room_slow | L | TRUE | 129 | 146 | 240 | 320 | -111 | -174 | 206.4 | 0.258 | 480 | 640 | 0.2825 | 0 | -0.3319 | 230
1777032124 | 0.291 | backlit_room_slow | L | TRUE | 125 | 165 | 240 | 320 | -115 | -155 | 193 | 0.2413 | 480 | 640 | 0.34 | 0 | -0.39 | 230
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

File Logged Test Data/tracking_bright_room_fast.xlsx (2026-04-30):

timestamp | elapsed_s | condition | active_cam | has_face | face_x | face_y | centre_x | centre_y | error_x | error_y | error_dist | norm_error_dist | frame_w | frame_h | l_pan_norm | r_pan_norm | tilt_norm | neck_ticks
1776991437 | 0.001 | bright_room_fast | L | TRUE | 88 | 192 | 240 | 320 | -152 | -128 | 198.7 | 0.2484 | 480 | 640 | 0.076 | 0 | -0.048 | 230
1776991437 | 0.166 | bright_room_fast | L | TRUE | 83 | 194 | 240 | 320 | -157 | -126 | 201.3 | 0.2516 | 480 | 640 | 0.1545 | 0 | -0.0953 | 230
1776991437 | 0.199 | bright_room_fast | L | TRUE | 84 | 194 | 240 | 320 | -156 | -126 | 200.5 | 0.2507 | 480 | 640 | 0.2325 | 0 | -0.1425 | 230
1776991437 | 0.25 | bright_room_fast | L | TRUE | 81 | 196 | 240 | 320 | -159 | -124 | 201.6 | 0.252 | 480 | 640 | 0.312 | 0 | -0.189 | 230
1776991437 | 0.304 | bright_room_fast | L | TRUE | 79 | 213 | 240 | 320 | -161 | -107 | 193.3 | 0.2416 | 480 | 640 | 0.392 | 0 | -0.2291 | 230
1776991437 | 0.372 | bright_room_fast | L | TRUE | 334 | 344 | 240 | 320 | 94 | 24 | 97 | 0.1213 | 480 | 640 | 0.345 | 0 | -0.2291 | 230
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

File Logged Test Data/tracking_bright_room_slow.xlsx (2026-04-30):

timestamp | elapsed_s | condition | active_cam | has_face | face_x | face_y | centre_x | centre_y | error_x | error_y | error_dist | norm_error_dist | frame_w | frame_h | l_pan_norm | r_pan_norm | tilt_norm | neck_ticks
1776990869 | 0.001 | bright_room | L | TRUE | 311 | 190 | 240 | 320 | 71 | -130 | 148.1 | 0.1852 | 480 | 640 | -0.0355 | 0 | -0.0488 | 230 | MAX | 0.2871
1776990870 | 0.121 | bright_room | L | TRUE | 310 | 190 | 240 | 320 | 70 | -130 | 147.6 | 0.1846 | 480 | 640 | -0.0705 | 0 | -0.0975 | 230
1776990870 | 0.171 | bright_room | L | TRUE | 311 | 190 | 240 | 320 | 71 | -130 | 148.1 | 0.1852 | 480 | 640 | -0.106 | 0 | -0.1462 | 230
1776990870 | 0.209 | bright_room | L | TRUE | 298 | 189 | 240 | 320 | 58 | -131 | 143.3 | 0.1791 | 480 | 640 | -0.135 | 0 | -0.1954 | 230
1776990870 | 0.246 | bright_room | L | TRUE | 287 | 196 | 240 | 320 | 47 | -124 | 132.6 | 0.1658 | 480 | 640 | -0.1585 | 0 | -0.2419 | 230
1776990870 | 0.311 | bright_room | L | TRUE | 262 | 215 | 240 | 320 | 22 | -105 | 107.3 | 0.1341 | 480 | 640 | -0.1585 | 0 | -0.2812 | 230
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

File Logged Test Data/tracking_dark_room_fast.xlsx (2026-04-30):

timestamp | elapsed_s | condition | active_cam | has_face | face_x | face_y | centre_x | centre_y | error_x | error_y | error_dist | norm_error_dist | frame_w | frame_h | l_pan_norm | r_pan_norm | tilt_norm | neck_ticks
1776991763 | 0.001 | dark_room_fast | R | TRUE | 159 | 328 | 240 | 320 | -81 | 8 | 81.4 | 0.1017 | 480 | 640 | 0 | 0.0405 | 0 | 230
1776991763 | 0.155 | dark_room_fast | R | TRUE | 167 | 371 | 240 | 320 | -73 | 51 | 89.1 | 0.1113 | 480 | 640 | 0 | 0.077 | 0.0191 | 230
1776991763 | 0.188 | dark_room_fast | R | TRUE | 187 | 362 | 240 | 320 | -53 | 42 | 67.6 | 0.0845 | 480 | 640 | 0 | 0.1035 | 0.0349 | 230
1776991763 | 0.231 | dark_room_fast | L | TRUE | 219 | 184 | 240 | 320 | -21 | -136 | 137.6 | 0.172 | 480 | 640 | 0 | 0.0994 | -0.0161 | 230
1776991763 | 0.261 | dark_room_fast | L | TRUE | 218 | 184 | 240 | 320 | -22 | -136 | 137.8 | 0.1722 | 480 | 640 | 0 | 0.0954 | -0.0671 | 230
1776991763 | 0.319 | dark_room_fast | L | TRUE | 217 | 184 | 240 | 320 | -23 | -136 | 137.9 | 0.1724 | 480 | 640 | 0 | 0.0916 | -0.1181 | 230
1776991763 | 0.383 | dark_room_fast | none | FALSE |  |  |  |  |  |  |  |  |  |  | 0 | 0.0916 | -0.1181 | 230
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

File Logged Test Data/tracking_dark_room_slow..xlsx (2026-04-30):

timestamp | elapsed_s | condition | active_cam | has_face | face_x | face_y | centre_x | centre_y | error_x | error_y | error_dist | norm_error_dist | frame_w | frame_h | l_pan_norm | r_pan_norm | tilt_norm | neck_ticks
1776991598 | 0.001 | dark_room_slow | L | TRUE | 183 | 214 | 240 | 320 | -57 | -106 | 120.4 | 0.1504 | 480 | 640 | 0.0285 | 0 | -0.0398 | 230
1776991598 | 0.15 | dark_room_slow | L | TRUE | 182 | 215 | 240 | 320 | -58 | -105 | 120 | 0.1499 | 480 | 640 | 0.0575 | 0 | -0.0791 | 230
1776991598 | 0.189 | dark_room_slow | L | TRUE | 180 | 216 | 240 | 320 | -60 | -104 | 120.1 | 0.1501 | 480 | 640 | 0.0875 | 0 | -0.1181 | 230
1776991598 | 0.246 | dark_room_slow | L | TRUE | 180 | 222 | 240 | 320 | -60 | -98 | 114.9 | 0.1436 | 480 | 640 | 0.1175 | 0 | -0.1549 | 230
1776991598 | 0.308 | dark_room_slow | L | TRUE | 184 | 237 | 240 | 320 | -56 | -83 | 100.1 | 0.1252 | 480 | 640 | 0.1455 | 0 | -0.186 | 230
1776991598 | 0.366 | dark_room_slow | none | FALSE |  |  |  |  |  |  |  |  |  |  | 0.1455 | 0 | -0.186 | 230
1776991598 | 0.429 | dark_room_slow | L | TRUE | 171 | 257 | 240 | 320 | -69 | -63 | 93.4 | 0.1168 | 480 | 640 | 0.18 | 0 | -0.2096 | 230
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

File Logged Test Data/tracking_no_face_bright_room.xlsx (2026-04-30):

timestamp | elapsed_s | condition | active_cam | has_face | face_x | face_y | centre_x | centre_y | error_x | error_y | error_dist | norm_error_dist | frame_w | frame_h | l_pan_norm | r_pan_norm | tilt_norm | neck_ticks
1776992113 | 0.001 | no_face | none | FALSE |  |  |  |  |  |  |  |  |  |  | 0 | 0 | 0 | 230
1776992113 | 0.09 | no_face | none | FALSE |  |  |  |  |  |  |  |  |  |  | -0.0005 | -0.0005 | 0 | 230
1776992113 | 0.124 | no_face | none | FALSE |  |  |  |  |  |  |  |  |  |  | -0.0015 | -0.0015 | 0 | 229
1776992113 | 0.171 | no_face | none | FALSE |  |  |  |  |  |  |  |  |  |  | -0.0029 | -0.0029 | 0 | 228
1776992113 | 0.215 | no_face | none | FALSE |  |  |  |  |  |  |  |  |  |  | -0.0048 | -0.0048 | 0 | 228
1776992113 | 0.282 | no_face | R | TRUE | 189 | 165 | 240 | 320 | -51 | -155 | 163.2 | 0.204 | 480 | 640 | -0.0046 | 0.0207 | -0.0581 | 228
1776992113 | 0.369 | no_face | none | FALSE |  |  |  |  |  |  |  |  |  |  | -0.0046 | 0.0207 | -0.0581 | 228
1776992113 | 0.446 | no_face | R | TRUE | 117 | 351 | 240 | 320 | -123 | 31 | 126.8 | 0.1586 | 480 | 640 | -0.0044 | 0.0822 | -0.0465 | 228
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

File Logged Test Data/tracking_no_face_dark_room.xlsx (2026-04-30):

timestamp | elapsed_s | condition | active_cam | has_face | face_x | face_y | centre_x | centre_y | error_x | error_y | error_dist | norm_error_dist | frame_w | frame_h | l_pan_norm | r_pan_norm | tilt_norm | neck_ticks
1776992532 | 0.001 | no_face_dim_room | none | FALSE |  |  |  |  |  |  |  |  |  |  | 0 | 0 | 0 | 230
1776992532 | 0.096 | no_face_dim_room | none | FALSE |  |  |  |  |  |  |  |  |  |  | -0.0005 | -0.0005 | 0 | 230
1776992532 | 0.132 | no_face_dim_room | none | FALSE |  |  |  |  |  |  |  |  |  |  | -0.0015 | -0.0015 | 0 | 229
1776992533 | 0.183 | no_face_dim_room | none | FALSE |  |  |  |  |  |  |  |  |  |  | -0.0029 | -0.0029 | 0 | 228
1776992533 | 0.245 | no_face_dim_room | none | FALSE |  |  |  |  |  |  |  |  |  |  | -0.0048 | -0.0048 | 0 | 228
1776992533 | 0.311 | no_face_dim_room | none | FALSE |  |  |  |  |  |  |  |  |  |  | -0.007 | -0.007 | 0 | 228
1776992533 | 0.379 | no_face_dim_room | none | FALSE |  |  |  |  |  |  |  |  |  |  | -0.0097 | -0.0097 | 0 | 227
1776992533 | 0.444 | no_face_dim_room | none | FALSE |  |  |  |  |  |  |  |  |  |  | -0.0127 | -0.0127 | 0 | 226
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

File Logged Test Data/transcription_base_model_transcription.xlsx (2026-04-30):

timestamp | condition | audio_duration_s | transcribe_time_s | realtime_factor | transcript
1777054605 | base_model_transcription | 5 | 4.26 | 0.852 | Hello Friday.
1777054627 | base_model_transcription | 5 | 4.01 | 0.802 | Good morning.
1777054651 | base_model_transcription | 5 | 4.03 | 0.806 | Nice powers.
1777054672 | base_model_transcription | 5 | 4.2 | 0.84 | Good night.
1777054690 | base_model_transcription | 5 | 5.07 | 1.013 | (clippers clattering) Your cute.
1777054711 | base_model_transcription | 5 | 3.65 | 0.73 | I like your feathers.
1777054733 | base_model_transcription | 5 | 3.79 | 0.758 | The weather is nice today.
1777054762 | base_model_transcription | 5 | 3.7 | 0.74 | What are you doing?
1777054780 | base_model_transcription | 5 | 3.79 | 0.758 | I am loving this.
1777054797 | base_model_transcription | 5 | 3.56 | 0.713 | I love red parts.
1777054815 | base_model_transcription | 5 | 4.25 | 0.85 | Can you tell me a joke about parrots?
1777054835 | base_model_transcription | 5 | 3.89 | 0.778 | how much more kind of wood chuck chuck?
1777054856 | base_model_transcription | 5 | 3.8 | 0.759 | I am from the beautiful tropical islands.
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

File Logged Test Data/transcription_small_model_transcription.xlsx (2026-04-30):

timestamp | condition | audio_duration_s | transcribe_time_s | realtime_factor | transcript
1777057112 | small_model_transcription | 5 | 16.9 | 3.38 | Hello, Freddy.
1777057141 | small_model_transcription | 5 | 14.46 | 2.892 | Good morning.
1777057169 | small_model_transcription | 5 | 14.02 | 2.803 | Nice palette.
1777057204 | small_model_transcription | 5 | 12.89 | 2.577 | (keyboard clicking) Good night.
1777057233 | small_model_transcription | 5 | 15.15 | 3.03 | [typing] You're cute.
1777057262 | small_model_transcription | 5 | 12.03 | 2.405 | I like your feathers.
1777057295 | small_model_transcription | 5 | 12.36 | 2.472 | The weather is nice today.
1777057321 | small_model_transcription | 5 | 12.12 | 2.425 | What are you doing?
1777057349 | small_model_transcription | 5 | 12.01 | 2.402 | I am loving this.
1777057378 | small_model_transcription | 5 | 12.32 | 2.465 | I love Red Parrots.
1777057408 | small_model_transcription | 5 | 13.04 | 2.609 | Can you tell me a joke about parents?
1777057441 | small_model_transcription | 5 | 13.17 | 2.633 | how much work can a woodchuck chuck?
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

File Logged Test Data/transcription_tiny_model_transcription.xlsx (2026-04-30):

timestamp | condition | audio_duration_s | transcribe_time_s | realtime_factor | transcript
1777056174 | tiny_model_transcription | 5 | 3.47 | 0.693 | Hello, baby.
1777056192 | tiny_model_transcription | 5 | 1.85 | 0.369 | Good morning.
1777056211 | tiny_model_transcription | 5 | 2.21 | 0.442 | Nice to meet you.
1777056226 | tiny_model_transcription | 5 | 1.92 | 0.384 | (water running)
1777056243 | tiny_model_transcription | 5 | 2.38 | 0.476 | [cough]
1777056268 | tiny_model_transcription | 5 | 2.31 | 0.462 | I like your fangirls.
1777056286 | tiny_model_transcription | 5 | 1.8 | 0.361 | Goodbye, that is nice to do.
1777056305 | tiny_model_transcription | 5 | 1.92 | 0.385 | What are you doing today?
1777056319 | tiny_model_transcription | 5 | 1.73 | 0.346 | I am loving this.
1777056337 | tiny_model_transcription | 5 | 1.65 | 0.33 | I love red parts.
1777056354 | tiny_model_transcription | 5 | 1.91 | 0.382 | Can you tell me a joke about parrots?
1777056374 | tiny_model_transcription | 5 | 3.42 | 0.684 | [Bell] How much will it kind of work shall I cut?
1777056394 | tiny_model_transcription | 5 | 1.88 | 0.375 | Bye, I'm family grateful tropical islands.
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

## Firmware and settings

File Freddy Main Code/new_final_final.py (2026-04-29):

"""
Freddy — Main Control Script
================================================
An animatronic parrot robot with:
  - Dual-camera face tracking (eyes & neck move)
  - Facial emotion detection with reactive behaviours
  - Wake-word ("Hey Freddy") triggered Parrot Mode
  - TTS with beak animation
  - Emotion-driven eyelid, wing, and LED behaviours
  - Scanning idle behaviour when no face is present
"""

import cv2
import warnings
warnings.filterwarnings("ignore", message="SymbolDatabase.GetPrototype")
import mediapipe as mp
import board
import busio
import time
import random
import threading
import csv
import datetime
from collections import deque, Counter
from hsemotion_onnx.facial_emotions import HSEmotionRecognizer
from adafruit_pca9685 import PCA9685
from picamera2 import Picamera2
import neopixel
import pyaudio
import pvporcupine
import numpy as np
import wave
import math
import re
import subprocess
import os
from better_profanity import profanity
from dotenv import load_dotenv

# Load environment variables from .env file
load_dotenv("/home/student/freddy/.env")


# =============================================================================
#  SECTION 1: CONFIGURATION FLAG
# =============================================================================

# Set True to write per-frame tracking and detection data to CSV files
# in the logging directory. 
# When enabled, the script will prompt for a test condition label at
# startup
#LOGGING_ENABLED = True
LOGGING_ENABLED = False

LOG_DIR = "/home/student/freddy/logs"


# =============================================================================
#  SECTION 2: HARDWARE SETUP
# =============================================================================

# ── MediaPipe face detection ─────────────────────────────────────────────────
# model_selection=0 selects the short-range model (faces within ~2 m),
# which suits Freddy's typical interaction distance for audio detection.
mp_face = mp.solutions.face_detection
mp_draw = mp.solutions.drawing_utils
face_detection = mp_face.FaceDetection(
    model_selection=0, min_detection_confidence=0.5
)

# ── PCA9685 servo driver ─────────────────────────────────────────────────────
# Details from Arduino servo starter code
i2c = busio.I2C(board.SCL, board.SDA)
pca = PCA9685(i2c)
pca.reference_clock_speed = 27_000_000
pca.frequency = 50


# =============================================================================
#  SECTION 3: SERVO CHANNEL DEFINITIONS & LIMITS
# =============================================================================
# Each servo has a channel on the PCA9685 and calibrated tick values for its
# mechanical limits.  Tick values were found experimentally per servo.

# ── Left eye ─────────────────────────────────────────────────────────────────
L_TILT_CH   = 5
L_TILT_UP   = 240
L_TILT_CEN  = 303
L_TILT_DOWN = 366

L_PAN_CH    = 6
L_PAN_LEFT  = 228
L_PAN_CEN   = 378   # intentionally matches RIGHT — mechanical range is one-sided
L_PAN_RIGHT = 378

# ── Right eye ────────────────────────────────────────────────────────────────
R_TILT_CH   = 9
R_TILT_UP   = 380
R_TILT_CEN  = 310
R_TILT_DOWN = 245

R_PAN_CH    = 10
R_PAN_LEFT  = 226
R_PAN_CEN   = 226   # intentionally matches LEFT — mechanical range is one-sided
R_PAN_RIGHT = 369

# ── Eyelids ──────────────────────────────────────────────────────────────────
L_EYELID_CH     = 4
L_EYELID_OPEN   = 320
L_EYELID_CLOSED = 225

R_EYELID_CH     = 8
R_EYELID_OPEN   = 283
R_EYELID_CLOSED = 380

# ── Neck ─────────────────────────────────────────────────────────────────────
NECK_CH    = 14
NECK_LEFT  = 180
NECK_CEN   = 230
NECK_RIGHT = 280

# ── Beak ─────────────────────────────────────────────────────────────────────
BEAK_CH     = 11
BEAK_CLOSED = 250
BEAK_OPEN   = 180

# ── Wings ────────────────────────────────────────────────────────────────────
L_WING_CH     = 0
L_WING_CLOSED = 280
L_WING_OPEN   = 183

R_WING_CH     = 15
R_WING_CLOSED = 311
R_WING_OPEN   = 418


# =============================================================================
#  SECTION 4: LED BELLY SETUP
# =============================================================================

PIXEL_PIN  = board.D18
NUM_PIXELS = 16
BRIGHTNESS = 0.2

pixels = neopixel.NeoPixel(
    PIXEL_PIN,
    NUM_PIXELS,
    brightness=BRIGHTNESS,
    auto_write=False,
    pixel_order=neopixel.GRB,
)

# LED colour per emotion (R, G, B) — chosen to be visually distinct and
# intuitively associated with each emotion.
EMOTION_LED_COLOURS = {
    "happy":    (255, 255,   0),  # yellow
    "sad":      (  0, 100, 255),  # blue
    "angry":    (255,   0,   0),  # red
    "surprise": (255,  20, 147),  # pink
    "fear":     ( 20,   0,  40),  # purple
    "disgust":  (  0, 180,   0),  # green
    "neutral":  (130,  35,   0),  # orange
    "unknown":  (  0,   0,   0),  # black
}

# Debug overlay colours (BGR for OpenCV)
EMOTION_COLOURS = {
    "happy":    (  0, 255, 255),  # yellow
    "sad":      (255, 100,   0),  # blue
    "angry":    (  0,   0, 255),  # red
    "surprise": (147,  20, 255),  # pink
    "fear":     (180,   0, 128),  # purple
    "disgust":  (  0, 180,   0),  # green
    "neutral":  (  0,  90, 200),  # orange
    "unknown":  (  0,   0,   0),  # black
}


# =============================================================================
#  SECTION 5: AUDIO & VOICE SETTINGS
# =============================================================================

# ── Porcupine wake word ──────────────────────────────────────────────────────
# Access key loaded from environment variable to avoid sharing sensitive information.
ACCESS_KEY   = os.getenv("PORCUPINE_ACCESS_KEY", "")
KEYWORD_PATH = "/home/student/freddy/hey_freddy.ppn"

# ── Recording settings ───────────────────────────────────────────────────────
FORMAT         = pyaudio.paInt16
CHANNELS       = 1
# How long Freddy listens after wake-word detection
LISTEN_SECONDS = 5.0            
OUTPUT_WAV     = "/home/student/freddy/command.wav"

# ── Whisper STT ───────────────────────────────────────────────────
# Using whisper.cpp for fast on-device inference.
# The --translate flag makes Whisper output English regardless of input language.
# The 'base' model was chosen as the best trade-off between accuracy and speed.
WHISPER_CLI     = "/home/student/freddy/whisper.cpp/build/bin/whisper-cli"
WHISPER_MODEL   = "/home/student/freddy/whisper.cpp/models/ggml-base.bin"
WHISPER_THREADS = "4"
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

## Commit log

2026-04-30 Create Servo_Calibration
2026-04-30 Uploading proj files
    [emotion_anger.csv, emotion_disgust.csv, emotion_fear.csv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]
